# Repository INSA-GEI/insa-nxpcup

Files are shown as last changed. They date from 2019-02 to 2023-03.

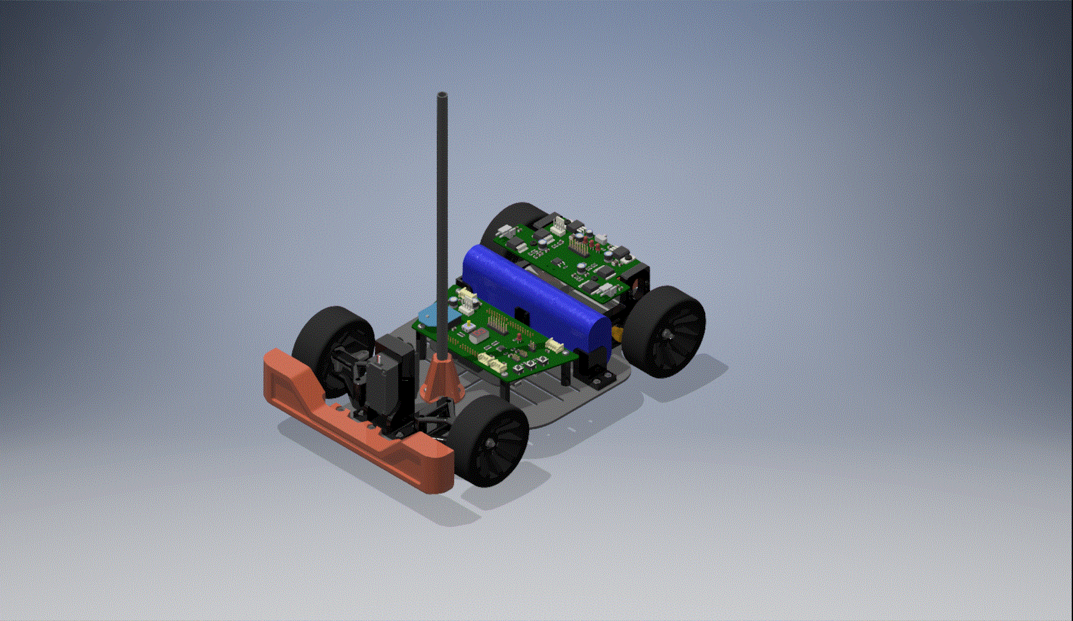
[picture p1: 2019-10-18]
meca/Inventor/Alamak.gif

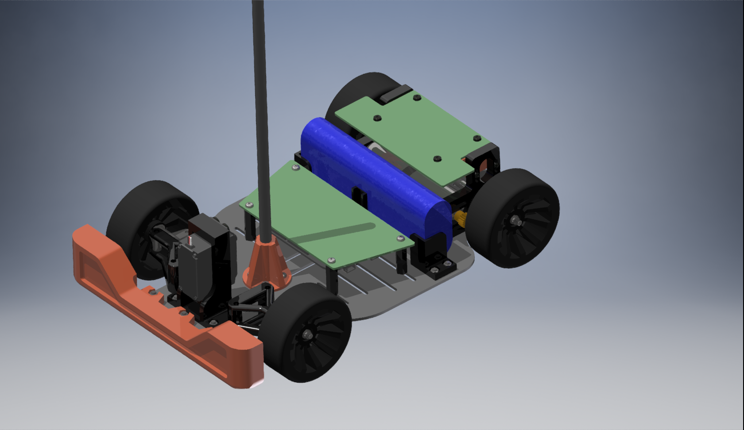
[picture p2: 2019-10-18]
meca/Inventor/Alamak.png

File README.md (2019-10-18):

# insa-nxpcup

Repository for INSA NXP cup 

# Where do I find/place the source code ?
Every folder titled `source_[...]` is a version of the code. One should only put the \*.c and the \*.h of the project, not the entire folder !

[...] Is a keyword or a_small_sentence describing this version in particular (e.g. "`source_dangerously_fast`" or "`source_safest`").

# Quick HowTo
Small survival kit for everyone : 
## Installing git (the clean way)
[Get here](https://git-scm.com/downloads) and follow the installer's instructions. One should avoid using github desktop client ;)

## Downloading the code
```bash
git clone https://github.com/INSA-GEI/insa-nxpcup-1.git
cd insa-nxpcup-1
```

## Update before you start working !
```bash
git pull 
```
If it doesn't work, save your changes elsewhere, and retry with
```bash
git stash	#Cancels all your changes in the repo
git pull	#Try pulling again
```

## Uploading your work
Upload as often as possible. Most errors here appear when working un un-updated code.
```bash
git commit -a #Prepare a commit with all updated files, ignoring new files.
git push #Sends the previous commit on this repo
```
**NB :** While commiting, use `Esc :wq Enter`. A good commit message is brief, and completes the following statement : *This commit will ...*.

# Branches management
**Do not use branches yet !**
Your are in branch master, nothing should be done here
Select a valid branch:

	git checkout int_team_1: Integration branch for team 1
	git checkout int_team_2: Integration branch for team 2

team work should use int_team_x branch as their main branch and integrate inside every stable work. Use development branch for your work in progress.

Old branchs:
	git checkout stable    : stable branch (Obsolete)
	git checkout dev       : work in progress (Obsolete)

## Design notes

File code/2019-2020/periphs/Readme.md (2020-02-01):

# Code de test des différents périphériques (low-level drivers) 
---
## test

Classe de debug ( UART OPENSDA, 7segment display, leds, rotary switch and pushbuttons).

Implémente un buffer circulaire et envoi par interruption.

##### TODO

* Solve issue with rotary switch missing counts -> check electrical continuity on pcb and correct port config
* Known issue with SW2 and BLUE_LED interferring : see pcb layout
* Extra : simplify usage of uart with a uart class in cpp

---
## Motor

Controle pwm des moteurs gauche et droit.

##### TODO

* Tabuler des vitesses en m/s pour diverses entrees en PWM (pour calibrer MOTOR_CAL_SPEED)

---
## Servo

Controle du servo avec limites d'angle.

##### TODO

* Check zero and max angle values

---

## encoder_v2

Retour de vitesse des roues

##### TODO

* Vérifier la bonne valeur de vitesse retournée par la classe pour une vitesse mesurée en réel

---

## Direction

Controlleur utilisant Motor, Servo, encoder_v2

##### TODO

* Calibrer coefficient entraxe
* calibrer correcteur KP
* vérifier la non saturation SPEED_LIMIT en fonctionnement normal

---
---

## Nom du dossier

Fonctions implementées

##### TODO

* Choses à faire
* ...

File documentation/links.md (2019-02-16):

# NXP community
* [git book nxp](https://nxp.gitbook.io/nxp-cup-hardware-reference-alamak/)
* [MCUXpresso example project with our board](https://github.com/ErichStyger/mcuoneclipse/tree/master/Examples/MCUXpresso/FRDM-KL25Z/MyMakeProject)
* [material ressources (sensors, motors, camera...)](https://community.nxp.com/docs/DOC-1284)
* [Landzo Alamak purchase website (for the fun)](https://www.aliexpress.com/store/product/Alamak-smart-car-competition-car-model-kit-CCD-camera-stand-base-Carbon-rod-bracket-8mm-base/428351_32817153828.html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)

# Misc.
* [ressources for robotics](https://github.com/Kiloreux/awesome-robotics#readme)

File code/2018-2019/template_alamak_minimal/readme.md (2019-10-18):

# Template alamak minimal 

Ce code est le template fournit par NXP permettant d'avoir une base en c pour tester la voiture

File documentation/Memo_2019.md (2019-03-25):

# Memo 2019
Voici nos notes à l'attention de l'équipe de l'INSA pour 2020. 

Il s'agit surtout d'une compilation de tous les problèmes que nous avons rencontré et qui auraient pu être évités.

## Problèmes de démarche et quoi faire

Pour avoir des informations concernant quoi faire, il ne faut absolument pas compter sur M.Tounsi. C’est mieux d’aller demander des infos à M.DiMercurio ou contacter kbkcao@etud.insa-toulouse.fr, saillan@etud.insa-toulouse.fr [ajoute des autres contacts]

Vous pouvez demander à M.Tounsi pour aller faire des tests de la voiture sur une piste à NXP de Toulouse. Normalement vous pouvez également emprunter les pistes et les ramener à l’INSA pour travailler avec. Nous avons travaillé en salle 113 puis salle 7.

## Problèmes de hardware

Les servos sur les voitures sont déjà remplacés par rapport à ce qui ont été utilisés en 2018. Les engrenages intérieurs des servos sont en métaux, plus costaud que ce que nous avions au début. Néanmoins, n’oublie pas de mettre des  pare-chocs en mousse devant les voitures quand vous travaillez à haute vitesse car une collision violente quand les voitures rament contre les murs, meubles, etc.... peut casser les engrenages intérieurs du servo.

Les cartes et les caméras sont assez fragiles et peuvent être facilement cramés donc il faut faire attention. Normalement M.DiMercurio peuvent refaire des PCB pour remplacer avec les schémas si ca n’est pas fait.

Il faut vérifier la transmission entre les moteurs et les roues derrières (pas trop serré car les moteurs pourront pas démarrer, mais si c’est pas assez proche il y aura pas de transmission).

L’idéal sera de changer les engrenages entre roues/moteurs. Pour l’instant il y a des engrenages plastiques contre d’autres en métaux. Il faudrait que tous soient au final en métal.

Il faut faire attention aux mâts de caméras, il faut vraiment fixer les caméras avant des faire les tests afin qu’elle ne tremble pas (sinon vous allez perdre de temps sur des trucs qui marchent par hasard). Il faut vraiment demander à M.Tounsi et M.DiMercurio pour faire en sorte que vous avez assez de voitures pour tester. Supposant que vous êtes aussi 3 équipes, il vous faut 3 voitures, et nous espérons de les voitures de notre année soient bien préservés pour que vous puissiez les ré-utiliser.

L’idéal est de vérifier le fonctionnement de la caméra avec un script simple sur matlab, il est également conseillé de bien faire la mise au point. Il est aussi possible de regarder les données renvoyées par la caméra en oscilloscope mais ca va être très difficile et ca marche pas tout le temps, donc c’est la dernière option. 

## Problèmes de software

Le caméra renvoie un array de 128 int de donnés. Pour visualiser “en live” le caméra il faut avoir une version Matlab craqué (version Matlab acheté il faut acheter le add-on Simulink Coder qui va couter 20e en plus, et on n’est pas trop sur quel autre add-on sera nécessaire) avec Simulink coder et les support packages faits pour le NXP cup. Concrètement les 3 add-ons: 

- NXP Cup Companion
- Simulink Coder Support Package for NXP FRDM-KL25Z Board
- NXP FRDM-KL25Z Support Package Update

Pour télécharger les packages il vous faut un compte Matlab. Ca marche même si vous avez un Matlab craqué. 
Par contre ca sera très difficile de faire marcher de manière optimale la voiture avec un program Matlab/Simulink, pour ca il faut vraiment hard-code un programme en C. Normalement les codes sont disponibles sur la page github de GEI.

Dernier point concernant l’histoire Matlab, il va vous sembler inutile de passer tous ces étapes juste pour visualiser les données du caméra, mais c’est très pratique: si qqch ne fonctionne pas, vous pouvez toujours voir ce que renvoie le caméra et fait un diagnostique en moins de 5 mins et vous serez pas bloqué des jours sur un caméra qui fonctionne pas.

Si vous travaillez sur une machine virtuelle Windows, les données observés avec le caméra sera pas très fiables. Il y a des guides et un fichier pré-fait pour observer les données du caméra dans les fichiers des add-ons. 

Pour programmer en C, il faut CodeWarrior. Vous pouvez trouver la version nécessaire ici: https://www.nxp.com/support/developer-resources/software-development-tools/codewarrior-development-tools/downloads:CW_DOWNLOADS 
Choisir la version: CodeWarrior® for MCUs (Eclipse IDE), version 11.1, Special Edition. Ce n’est pas payant et il faut juste faire un compte NXP. 

Les programmes qui fonctionnent sont normalement sur Github de GEI, NXP Cup et vous pouvez demander à M.DiMercurio de vous ajouter pour avoir accès à ces fichiers. Il est fortement conseillé de savoir utiliser le github car nous ne l'avons pas assez utilisé et c’est un peu un bordel le projet. Gros avantage de Github: dès que vous avez un truc qui fonctionne bien et vous êtes satisfait, faites un push avant de continuer car **LE MÊME CODE VA PAS FONCTIONNER PAREIL APRÈS 30 MINS ET QUELQUES CHANGEMENTS DE VARIABLES.** N'hésitez pas à rajouter 'STABLE' dans votre message de commit quand le code marche.

## Problèmes liés aux tests

Il faut nettoyer les roues de la voitures et les pistes/ la salle car le frottement va beaucoup changer le comportement de la voiture. Si vous travaillez en salle 7 (qui est très salle et a beaucoup de poussière), il faut passer aspirateur ou passer un coup de balaie, ensuite nettoyer la salle avec une serpière pour réduire au minimum la poussière). Comme ca on peut être sur que les roues va adhérer à la piste. Il faut faire le nettoyage régulièrement!! (au début de votre séance de test). Niveau de propreté recommandé: vous pouvez marcher à pieds nus confortablement dans la salle. 

Comme mentionné avant, il faut faire attention quand on fait des testes à haute vitesse car ca peut endommager des servos quand les voitures rament contre les meubles, la voiture peut passer en dessous les meubles et il y a des barres qui va casser les mâts de caméras. Les mâts peuvent être refaits mais les caméras sont un peu cher et difficile de retrouver (nous avons du aller sur eBay pour trouver un remplacement) et donc il faut faire attention. 

Il y a beaucoup de paramètres qui influencent le comportement de la voiture (les seuils pour détection des gradients de luminosité, les valeurs de correcteurs, combien de correcteurs, frottement, etc...) Change un seul truc à la fois et voit comment comporte la voiture. Avoir aussi des priorités, par exemple: si vous êtes pas surs que vos caméras fonctionnent correctement et plus ou moins résilients contre les variations de luminosité, si votre servo n’est pas bien polarisé, etc... ca vaut pas la peine d’aller chercher les paramètres de correcteurs car ca va pas remarcher. 

C’est normal qu’un truc qui fonctionne aujourd’hui ne fonctionne plus le lendemain (même au bout d’une heure). Il faut vraiment aller chercher pourquoi et régler le problème pour vraiment bien avancer.

## Recommandations

Ajouter un panneau de LEDs pour éclairage, ca va aider à régler le problème de seuil de caméra. L’idéal est d’avoir une forte lumière rouge pile à l’endroit qu’observe la caméra. Cela vous permettra d’avoir un programme robuste qui fonctionnera peut importe l’éclairage ambiant. (nous sommes partis du principe que l’éclairage lors de la compétition serait optimal et cela a été une grosse erreur).

On a des encodeurs pour avoir une régulation de vitesse. Ca peut beaucoup améliorer votre commande de vitesse mais ne perdez pas trop de temps là-dessus si vous arrivez pas.
Il peut être très pertinent d’utiliser 2 caméras (une qui regarde loin et une qui regarde proche). Cela permettra d’aller encore plus vite en ligne droite tout en anticipant les prochains virages.

Si vous avez du temps, vous pourrez peut être étudier comment utiliser une caméra 2D. Un exemple c’est le ligne d’arrivé qui peut être très difficile à détecter avec une seule caméra ligne. 

Vous pouvez ajouter des autres capteurs pour finir des challenges (si il y a encore des challenges pour NXP Cup 2020). Ex : capteur de distance

Il peut être intéressant d’utiliser les accéléromètres présents sur le microcontrôleurs. Cela permettra de détecter le passage d’un “bump” et d’ignorer les données inexploitables renvoyées par la caméra à ce moment là

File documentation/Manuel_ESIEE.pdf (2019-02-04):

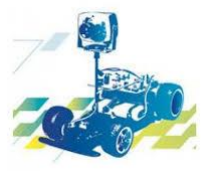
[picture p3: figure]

# Guide de de marrage et de de veloppement pour la NxP Cup

Pour châssis Model-C et carte microcontrôleur FRDM KL25Z

T. Grandpierre (t.grandpierre@esiee.fr)

T. Grandpierre © / ESIEE | 2

T. Grandpierre © / ESIEE | 3

## Remerciements

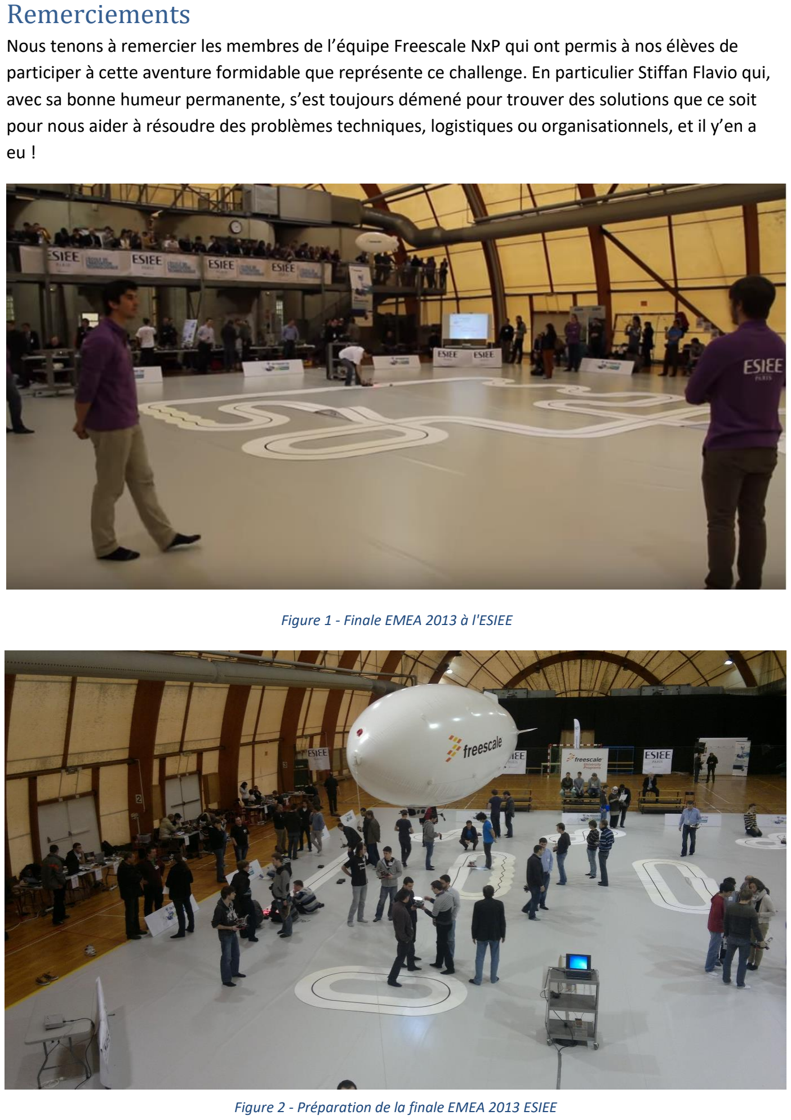
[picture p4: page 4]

Nous tenons à remercier les membres de l’équipe Freescale NxP qui ont permis à nos élèves de participer à cette aventure formidable que représente ce challenge. En particulier Stiffan Flavio qui, avec sa bonne humeur permanente, s’est toujours démené pour trouver des solutions que ce soit pour nous aider à résoudre des problèmes techniques, logistiques ou organisationnels, et il y’en a eu !

Figure 1 - Finale EMEA 2013 à l'ESIEE

Figure 2 - Préparation de la finale EMEA 2013 ESIEE

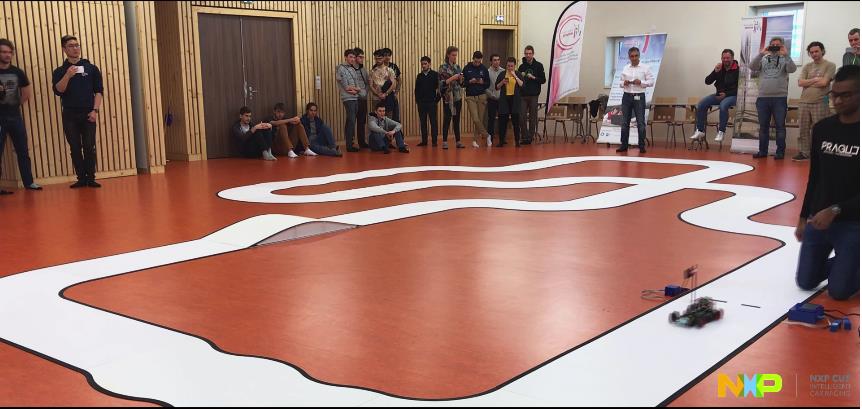
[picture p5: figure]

T. Grandpierre © / ESIEE | 5

## Introduction

### Présentation

La NxP Cup est une compétition mondiale qui commence par des sélections dans chaque continent. C’est une course de voiture miniatures autonomes sur un circuit qui n’est pas connu à l’avance. Le circuit est matérialisé par deux lignes noires tracées sur une bande blanche. Il peut y avoir des croisements, des ponts, des ralentisseurs, des tunnels.

Le châssis (groupe de propulsion et direction) est imposé, mais le choix de la carte de contrôle (microcontrôleur NxP) et des capteurs est libre. L’objectif est donc de construire une voiture qui soit autonome et roule le plus vite possible en détectant la piste.

Figure 2 - Vidéo complète : https://perso.esiee.fr/~antonraj/mes_projets/Nxp_cup/wp-content/video/nxp_cup_2018_esiee.mp4

La page principale de présentation de la NxP Cup où toutes les infos sont données : https://community.nxp.com/groups/tfc-emea

EMEA : region Europe, Middle-East (Moyen-Orient), Africa.

### Intéret pédagogique

- Travailler en équipe
- Réalisation complète

T. Grandpierre © / ESIEE | 6
- Prog. des microcontrôleurs (langage C) + programmation PC
- Electronique (contrôle moteur, caméra, radio...)
- Apprendre à résoudre des problèmes concrets
- Sujet transversal, robotique
- Autonomie
- Découverte, contacts avec le monde industriel, les contraintes, les délais

### Principe

Il faut identifier en temps réel les bords de la piste qui sont tracés en noir sur fond blanc. Il existe plusieurs solutions pour cela : utilisation de caméras noir et blanc ou couleur, utilisation de caméras linéaires, utilisation d’une barre de capteur infra-rouge…

L’utilisation d’une barre est peu appropriée car encombrante. En effet elle doit être disposée juste au-dessus de la bande noire, de plus la sensibilité et la précision seront assez faible.

L’utilisation d’une caméra 2D standard noir et blanc ou couleur est idéale mais demande une relativement forte puissance de calcul embarquée ainsi que de la mémoire RAM pour stocker la ou les images : jusqu’en en 2017 seul certain microcontrôleurs étaient autorisés ce qui limitait cette possibilité relativement complexe.

L’utilisation d’une caméra linéaire est très adaptée, elle est fournie dans le kit de démarrage NxP.

### Kit de démarrage NxP

Jusqu’en 2017, le seul châssis autorisé était le « modèle-C », celui dont on dispose à l’ESIEE :

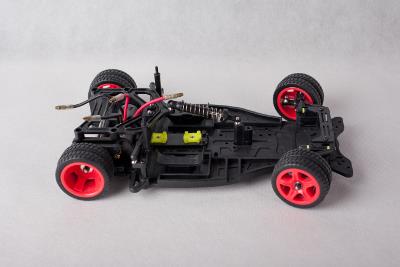
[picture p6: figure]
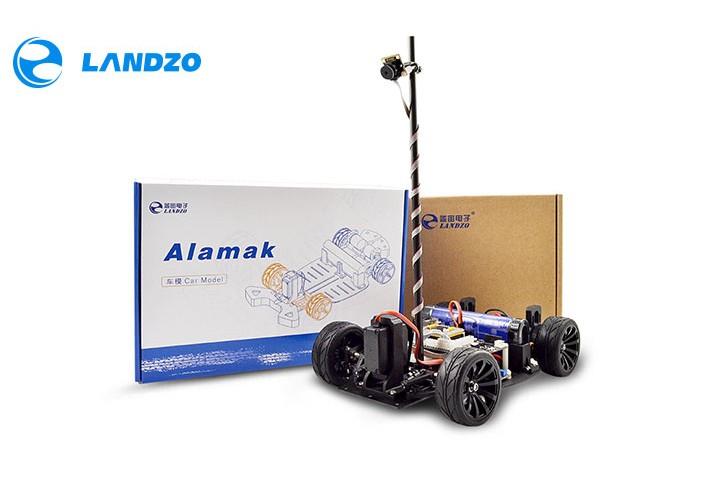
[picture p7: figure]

T. Grandpierre © / ESIEE | 7

Figure 3- Châssis "Model C"

Depuis 2017 un nouveau châssis a vu le jour et fait l’objet d’une course spécifique, le modèle « Alamak » :

Figure 4- Châssis « Alamak »

Ces châssis comportent 2 moteurs à balais 7.2v maximum pour la propulsion et un servomoteur standard de modélisme pour la direction.

Pour piloter le servo et les moteurs, NxP a développé des cartes d’interface de puissance (2 versions successives pour le modèle C et une nouvelle version pour le modèle Alamak). Ces cartes offrent les mêmes fonctionnalités : elles comportent des ponts en H pour la commande des moteurs de propulsion et la connectique pour une ou deux caméras linéaires et pour un ou deux servo de direction.

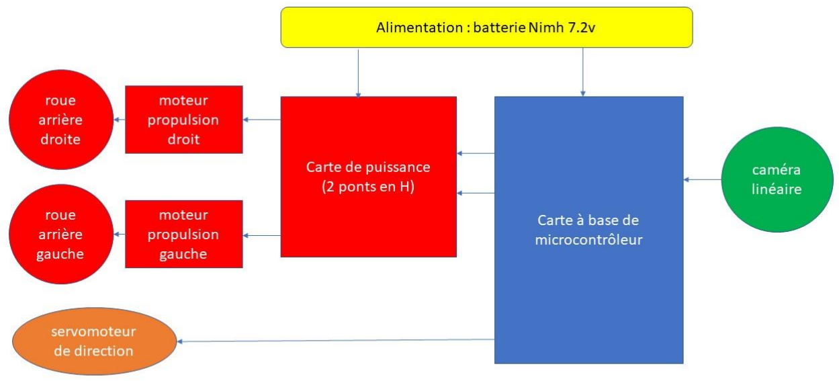
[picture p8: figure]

T. Grandpierre © / ESIEE | 8

Enfin, pour « l’intelligence » de la voiture, NxP propose plusieurs kits de développement à base de leurs microcontrôleurs : Kinetis FRDM-KL 25Z, TWR-K40X256, Qoriva MPC-5604B, K40 KwikStik…

La page suivante regroupe des liens vers les différentes options possibles pour le matériel : https://community.nxp.com/docs/DOC-1284

### Architecture d’une voiture

Un véhicule est donc composé au minimum des éléments suivants :

- Un châssis « Alamak » ou « model C »
- 2 moteurs de propulsion
- 1 servo de direction
- Une carte de puissance pour les moteurs de propulsion
- Une caméra linéaire
- Une carte microcontrôleur
- Une batterie Nimh 7.2v 2500mAh max (imposé)

Figure 5 -Architecture fonctionnelle de la voiture

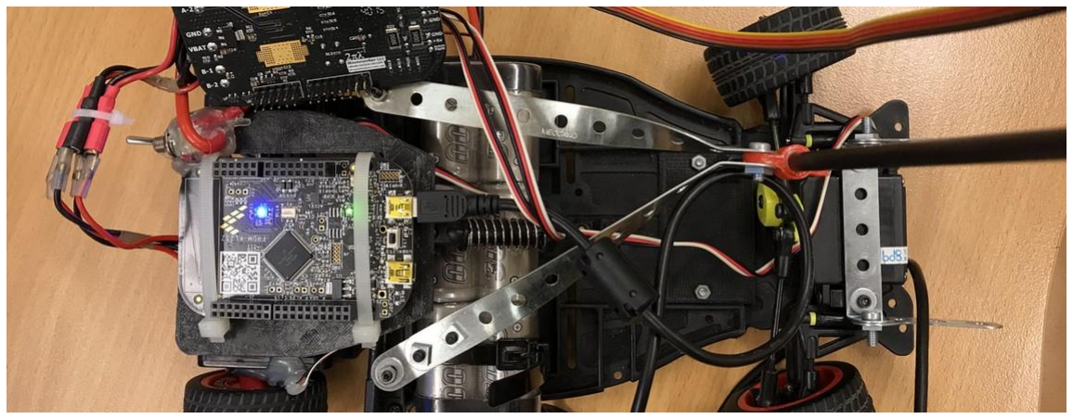
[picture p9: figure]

T. Grandpierre © / ESIEE | 9

Choix du matériel ESIEE :

- Châssis « modèle C »,
- Cartes microcontrôleurs FRDM-KL25Z (et KL46Z plus puissantes dont les connecteurs sont compatibles),
- Cartes filles de puissance compatible FRDM-KL25Z (rev. 1 : https://community.nxp.com/docs/DOC-1059 )
- Caméra linéaire « TAOS 1401 » ( https://community.nxp.com/docs/DOC-1030 )

Figure 6 - Carte KL25Z sur châssis « modèle C »

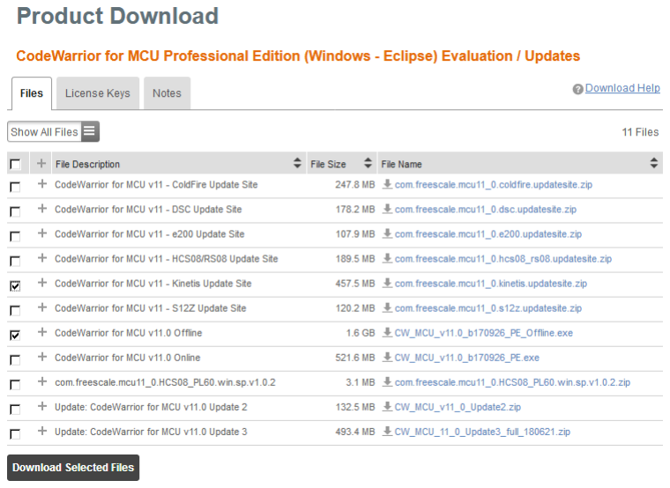
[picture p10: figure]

T. Grandpierre © / ESIEE | 10

## Prise en main Kinetis KL25Z

Avant de pouvoir utiliser la carte de développement FRDM-KL25Z, nous commençons par présenter l’installation de l’environnement, puis nous présentons la carte, comment la configurer avant de terminer par la présentation d’un exemple complet qui fait clignoter ses leds.

### Environnement de développement logiciel

Sous windows : 3 grandes possibilités Code Warrior (l’IDE Freescale), Kinetis Studio, ou Keil-MDK µVision. Ils permettent tous de saisir du code C/asm, de le compiler, de le télécharger sur le micro, de faire du débug pas à pas.

1. Code Warrior 10.6, 10.7 ou 11 (« CW ») : c’est l’outil de dev. Freescale/NxP , l’avantage quand on l’installe c’est que l’on va disposer des exemples freescale pour chacune des cartes. Les versions 10.6 et 10.7 sont les anciennes versions de CW (voir 2.) utilisées pour créer les exemples pour la voiture. La version 11 semble aussi le permettre, à vérifier.
a. « CodeWarrior 11 » est téléchargeable en version d’évaluation ici : https://nxp.flexnetoperations.com/control/frse/download?element=9346447
Il faut sélectionner l’extension pour Kinetis :
b. « CodeWarrior MCU v10.6 Evaluation Edition » la version complète limitée à 1 mois qui devient limitée en taille de binaire généré quand le mois est écoulé.
c. « CodeWarrior MCU v10.6 Special Edition » la version illimitée en durée mais limitée en taille. Je vous conseille d’utiliser celle-ci, puis plus tard si vous êtes limité par les 128Ko ( !!), d’installer la version Evaluation Edition.
Remarque importante : les versions CW 10.6 et 10.7 ont été conçues avant Win7, le répertoire d’installation des programmes s’appelait alors « c:\Program Files », il n’y

T. Grandpierre © / ESIEE | 11

avait pas de répertoire « c:\programme file x86 » dans lequel s’installent par défaut tous les softs 32bits => ATTENTION si possible installer CW dans c:\Program Files car si il est installé ailleurs des exemples risquent de ne pas fonctionner car les includes sont parfois codés en dur. Cependant pour mes tests tout s'est bien passé en l'installant dans c:/freescale/CW etc.

2. Kinetis Studio : il a été un temps le successeur de CodeWarrior pour la gamme des microcontrôleurs Kinetis, mais je pense finalement en voie d’abandon pour revenir à CodeWarrior 11.0 for MCU
3. Keil MDK µVision est l’outil supporté par ARM pour tous les micros de la famille des cortex M : Freescale (Kinetis), NXP (LPC), STM (32F 32L), Texas Instrument (Stelaris, Tiva) etc.). Son IDE est très simple et très rapide à prendre en main (c’est celui que nous utilisons pour nos TPs d’introduction aux Cortex M à l’ESIEE en première année). Comme CW, il existe en version limitée (MDK-Lite) en taille de code généré mais seulement 32Ko (ce qui est quand même largement suffisant pour les premiers projets). Il est téléchargeable depuis cette page, il faudra remplir un formulaire : http://www.keil.com/arm/mdk.asp Il est intéressant de le connaitre pour passer d’un constructeur à l’autre. De plus, il est fourni avec au moins un exemple (clignotement d’une led) pour quasiment toutes les cartes de dev. de tous les constructeurs. Il est aussi très intéressant en pédagogie car il contient aussi un simulateur assez complet permettant entre autre de voir les GPIO et autres périphériques (attention cependant, ce simulateur n’existe pas pour toutes les variantes de micro/constructeur, pour un constructeur donné il faut chercher la référence de la variante pour laquelle il existe un simulateur).

Le projet de démonstration fournit par NxP pour tester la voiture étant sous Code Warrior, nous choisissons donc

### Présentation de la carte de développement « Freedom » FRDM-KL25Z

Le microcontrôleur à programmer est au centre « KL25Z ». « 80 LQFP » correspond au type du boitier (LGFP) et au nombre de broches (80). Il est en effet plusieurs variantes de ce processeurs avec plus ou moins de broche et donc des types de boitiers plus ou moins gros.

Pour mieux comprendre cette carte il faut analyser son manuel utilisateur et ses schémas disponibles dans l’archive suivante (chercher « frdm kl25z sur le site NxP), puis cliquez sur « User Guide »:

https://www.nxp.com/support/developer-resources/evaluation-and-development-boards/freedom-development-boards/mcu-boards/freedom-development-platform-for-kinetis-kl14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 (https://www.nxp.com/support/developer-resources/evaluation-and-development-boards/freedom-development-boards/mcu-boards/freedom-development-platform-for-kinet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)

T. Grandpierre © / ESIEE | 12

Figure 7- Carte FRDM-KL25Z -Vu côté composants

On constate que la carte comporte :

- une led RGB (constituée de trois leds dans un même boitier),
- un capteur inertiel MMA8451Q (accéléromètre)
- un « slider » tactile capacitif (en haut)
- 2 connecteurs USB,
- 4 connecteurs d’entrées-sortie de chaque côté (J1, J2, J9 et j10).

Le rôle de ces connecteurs est récapitulé dans la figure page 14 :

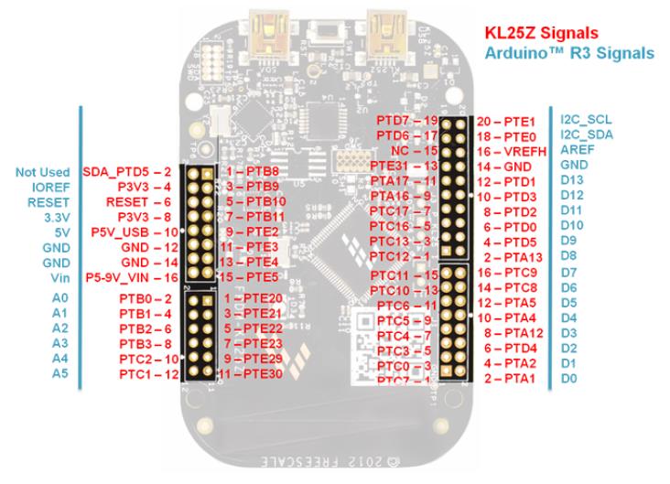
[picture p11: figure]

T. Grandpierre © / ESIEE | 13

On constate ainsi que la disposition des broches est faites pour être compatible (en bleu) au maximum avec le brochage des cartes filles (« shield ») Arduino.

Le « block diagram » (figure suivante extraite de la page 4 du « user manual ») nous apprend que le KL25Z est un KL25Z128VLK4 80 LQFP », et qu’il est alimenté par les deux connecteurs USB par le biais d’un convertisseur 3,3v à faible perte (en rouge) mais alimentable aussi par l’un des connecteurs (vin).

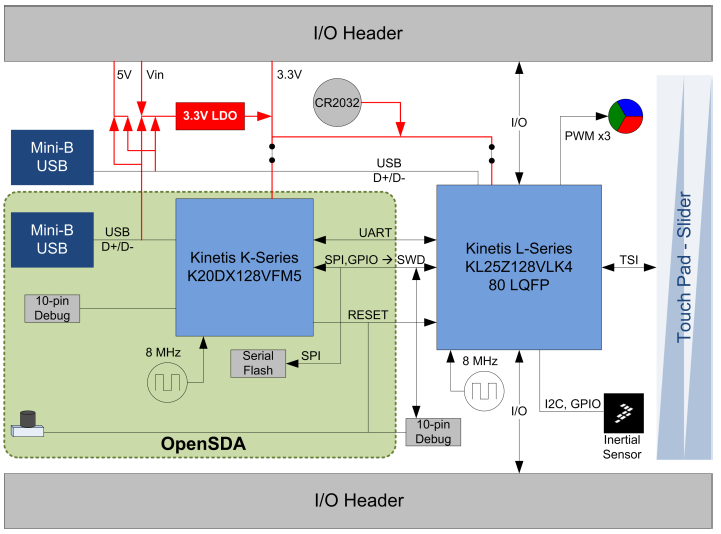
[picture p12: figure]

T. Grandpierre © / ESIEE | 14

Figure 8 - Architecture de la carte FRDM-KL25Z

On y découvre aussi que les cartes Kinetis possèdent une interface de débogage incorporée : via une connexion USB entre le PC (qui exécute Code Warrior) et la carte il est possible de télécharger du code dans la RAM ou la FLASH du microcontrôleur KL25Z et ce sans matériel supplémentaire. C’est la partie sur fond vert de la figure ci-dessus suivante.

Cette interface de programmation fonctionne selon un protocole série appelée « OpenSDA ». Il utilise un autre microcontrôleur (K20DX128VFM5) dédié à cet usage uniquement. Pour travailler sur cette carte depuis le PC il faut donc connecter un câble USB entre le PC et le connecteur USB mini marqué « OpenSDA » (c’est-à-dire celui de droite sur la photo page précédente).

### Configuration de la carte pour mode debug

Par défaut, quand la carte est neuve la carte elle est préprogrammée avec une démo qui fait varier les couleurs des leds en fonction de la position spatiale de la carte, mesurée à l’aide du capteur inertiel.

De plus, en connectant cette carte au PC (après avoir éventuellement installé les drivers) on constate que le microcontrôleur secondaire (K20DX128) n’est pas en mode OpenSDA mais émule une carte mémoire ( firmware « mass storage ») : la carte est alors vue par le PC comme une clef USB. C’est très intéressant car pour placer une application dans la carte depuis windows il suffit de copier/coller le binaire de cette application (fichier d’extension .sc) dans cette « clef usb ». C’est donc très simple, NxP fournit ainsi plusieurs programme compilé dans le sous-répertoire « Precompiled Examples » de

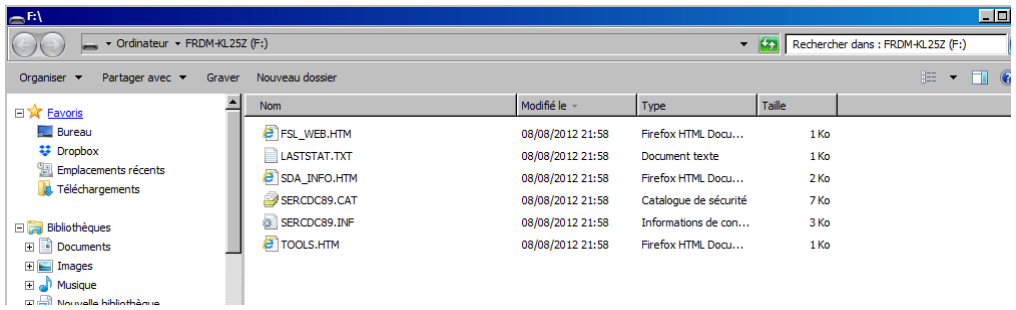
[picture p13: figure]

T. Grandpierre © / ESIEE | 15

l’archive « FRDM-KL25Z Quick Start Package » téléchargeable sur la page NxP dédié à cette carte. Remarque : ne pas copier directement les fichiers entre l’application d’archivage et la clef, il est préférable de d’extraire les fichiers avant de la placer sur la carte.

Figure 9 - FRDM-KL25Z vue par le PC comme une clef USB de même nom

En revanche dans ce mode, il n’est pas possible de faire du débogage. Pour la passer en mode débogage « OpenSDA » il faut reflasher le firmware du microcontrôleur K20 (pas le KL25Z) de la carte, ceci compte plusieurs étapes :

1. Tout d’abord il faut récupérer le firmware qui est développé par PEMICRO (partenaire de NxP). Le lien peut être obtenu en cliquant directement sur le fichier « SDA_INFO.HTM » présent sur la carte (voir figure précédente) , ou bien en allant sur leur site : http://www.pemicro.com/opensda/index.cfm Il faut alors télécharger le fichier archive de la section « OpenSDA Firmaware » (« Firmware Apps ») : Pemicro_OpenSDA_Debug_MSD_Update_Apps..date...zip. Cette archive contient les firmwares pour plusieurs cartes de développement, il faut extraire les 2 fichiers qui correspondent à notre FRDM-KL25Z, c’est-à-dire : DEBUG-APP_Pemicro_v108.SDA et si besoin MSD-DEBUG-FRDM-KL25Z_Pemicro_v118.SDA qui est le firmware d’origine si l’on voulait remettre la carte dans le mode « Mass Storage ».
2. Ensuite il faut placer la carte en mode « Firmware update », pour cela :
a. Débrancher le câble USB de la carte
b. Appuyer sur le bouton poussoir de la carte
c. Reconnecter le câble USB sur le même port USB (OpenSDA) en maintenant toujours le bouton poussoir appuyé
d. Relâcher le bouton poussoir après quelques secondes
3. La carte devrait être vu maintenant comme une clef USB dont le nom n’est plus KL25Z comme précédemment, mais « BOOTLOADER »

T. Grandpierre © / ESIEE | 16

Figure 10- La FRDM-KL25Z apparait comme une clef USB « BOOTLOADER »

4. Il suffit de placer le fichier de firmware (DEBUG-APP_Pemicro_v108.SDA) sur ce nouveau lecteur, attendre 1 minute pour être certain que la mise à jour s’effectue,
5. puis brancher/rebrancher l’USB (sans appuyer sur le poussoir puisque le firmware est maintenant à jour).
6. Cette fois, plus aucune fenêtre ne doit s’ouvrir, la carte n’est plus vue comme une clef USB mais comme une interface de programmation OpenSDA (voir ci-dessous), mais pour cela il peut être nécessaire d’installer le driver windows de cette interface de programmation OpenSDA : sur la même page PEMICRO où les drivers ont été trouvés, il y a une rubrique
« Windows USB Drivers » avec un exécutable (.exe) qu’il faut exécuter. Débrancher la carte avant de l’exécuter.
7. Il est toujours préférable de s’assurer que la carte est bien configurée en mode OpenSDA et que le driver est bien installé. Pour cela il faut ouvrir le « gestionnaire de périphériques » (taper son nom dans la barre de recherche windows), et dans la rubrique « Ports (COM et LPT) » vous devez voir apparaitre « OpenSDA » ainsi que le numéro de port série associé (COM35 dans la capture ci-dessous) :

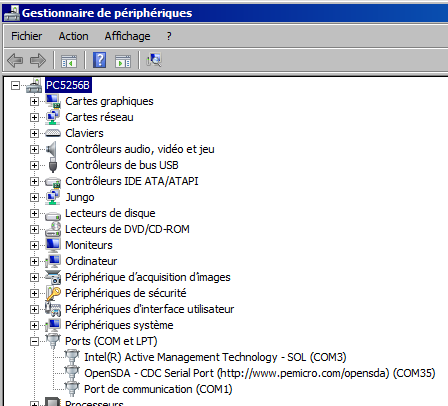
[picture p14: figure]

T. Grandpierre © / ESIEE | 17

Figure 11- Gestionnaire de périphériques

REMARQUE WINDOWS 10 : sous windows 10, en fonction des versions, il se peut que les transferts vers la carte ne fonctionne pas, que ce soit en mode « Mass Storage » ou en mode de mise à jour du bootloader. Cela est dû au fait que windows 10 créé des fichiers cachés d’indéxation et qu’ils sont aussi copiés sur la carte. Pour que cela fonctionne sous windows 10, il faut utiliser une des trois solutions suivantes après avoir lancé le gestionnaire de services (« services.msc »), puis désactivé le service de stockage et windows search :

- 1

ère possibilité : éditeur de statégie

Lancer l’éditeur de stratégie (« gpedit.msc »), puis aller dans « Config. De l’ordinateur »➔ « modèle d’administration »➔composants windows ➔ Rechercher et cliquer sur la politique « Ne pas autoriser d’emplacement sur les disques amovibles aux bibliothèques », activer cette politique et OK. Redémarrer le PC.

- 2

ème possibilité : éditeur de registre

Lancer l’éditeur de registre (« regedit »), puis chercher l’une clefs « search » ou « windows search » qui contient la propriété « DisableRemovableDriveIndexing » qu’il faut passer à 1.

T. Grandpierre © / ESIEE | 18

Si elle n’existe pas vous pouvez la créer dans "HKEY_LOCAL_MACHINE\SOFTWARE\Policies\Microsoft\Windows Search". Puis ajouter une clef nommée "DisableRemovableDriveIndexing" avec le type "REG_DWORD" et la placer à
1. Redémarrer le PC.
- 3

ème possibilité : trouver une machine windows 7 pour changer le firmware en OpenSDA. Une fois le changement effectué, il n’y a plus de problème liés à windows 10.

(voir https://os.mbed.com/users/maripogoda/notebook/update-frdm-kl25z-bl-with-win8/ pour des informations complémentaires).

### Premier programme « From Scratch » avec Code Warrior

Lancer Code Warrior. Comme tous les outils basés sur l’environnement Eclipse il vous demande de choisir l’emplacement d’un espace de travail « worspace », vous pouvez laisser celui par défaut ou le renommer par exemple « KL25Workspace ». Ainsi vous pourrez switcher d’une espace à un autre facilement si vous avez plusieurs projets.

Ensuite il suffit de créer un nouveau projet : menu new→BareBoard Project et choisir le processeur qui correspond à la carte cible en regardant sa référence, tout simplement :

Figure 12- Reference du processeur KL25Z128

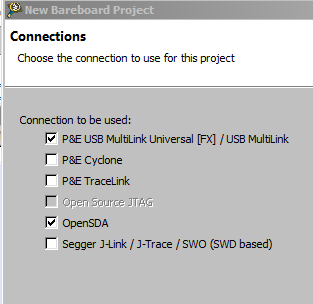
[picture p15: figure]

T. Grandpierre © / ESIEE | 19

Choisir ensuite la connexion OpenSDA

Puis laisser les configurations proposées par défaut sur les onlgets qui suivent jusqu’à cliquer sur « Finish ».

Code Warrior génère alors un projet de base avec un fichier main.c contenant une boucle infinie :

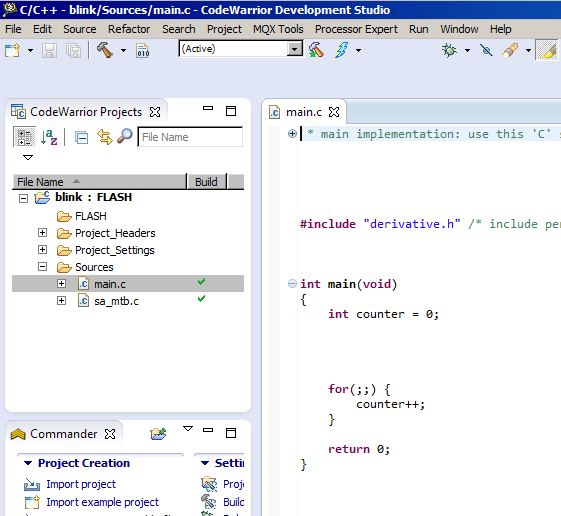
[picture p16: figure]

T. Grandpierre © / ESIEE | 20

Vous devez pouvoir le compiler sans erreur en cliquant sur le marteau de la barre de menu. Il faut ensuite le transférer dans la mémoire de votre carte en cliquant sur le petit insecte vert. CW communique alors avec votre carte (qui doit être connectée par USB !), prend le contrôle du processeur et y télécharge votre programme dans sa mémoire RAM. Cliquer enfin sur le rectangle vert pour lancer l’exécution. Bravo, le programme tourne….mais comment le savoir ? Faites pause (bouton à gauche du rectangle rouge) . Ceci stoppe le processeur et lit la valeur des variables de votre programme (la valeur de counter s’affiche en haut à droite) :

et une flèche vous indique là où s’est arrêté le processeur :

T. Grandpierre © / ESIEE | 21

Vous pouvez relancer/arrêter à nouveau pour vérifier les incréments du compteur :

Figure 13- nouvelle valeur du compteur

Oui, il compte très vite : à 48 MHZ !

Vous pouvez mettre fin à la session de debbug en cliquant sur le rectangle rouge, puis revenir dans le projet en cliquant sur « C/C++ » dans la barre du haut à droite.

Notez que ce programme inclut un fichier « derivative.h » qui lui-même inclut un fichier
<MKL25Z4.h> (faites simplement un clic droit sur le nom pour ouvrir le fichier). Parcourez ce dernier pour découvrit qu’il contient les définitions des adresses de tous les registres internes du processeur, cela va s’avérer très pratique pour la section suivante !

### Faire clignoter une led

C’est le « hello world » de l’embarqué, on commence souvent par allumer une led pour tester la chaîne de développement. Sur cette carte il y a 3 leds dans un même boitier, choisissons de faire clignoter la rouge (vous pourrez changer facilement !).

Pour l’allumer, il faut l’identifier sur le schéma du « User manual » de cette carte ( p.13) ou directement dans le pdf contenant ces schémas : FRDM-KL25Z_SCH_REV_E.pdf page 3 en bas à gauche :

T. Grandpierre © / ESIEE | 22

Les leds rouge, verte et bleu sont respectivement connectées sur le bit 18 du port B, le bit 19 du port B et le bit1 du port D.

En suivant le nom du fil on trouve même le numéro des broches du KL25Z : 53 pour PTB18 et 54 pour PTB19.

En cherchant cette broche sur la data sheet page du processeur (KL25P80M48SF0.pdf), on découvre (p48 de KL25P80M48SF0.pdf et dans la colonne « 80 LQFP » puisque c’est le suffixe de la référence de notre processeur soudé sur cette carte, cela correspond au nombre de broches) que cette broche peut être configurée pour l’une des deux fonctions : PTB18 (colonne ALT1) ou TMP2_CH0 (colonne ALT 3).

En effet, en lisant le référence manuel (KL25P80M48SF0RM.pdf ) et en particulier le chapitre 11 « Port control and interrupts) , on découvre qu’il est possible de choisir le périphérique auquel on veut connecter la broche en fonction de la valeur « ALT » qu’il faut placer dans les bits 10 à 8 du registre « Pin Control Register n », communément appelé « PORTx_PCRn » (p184).

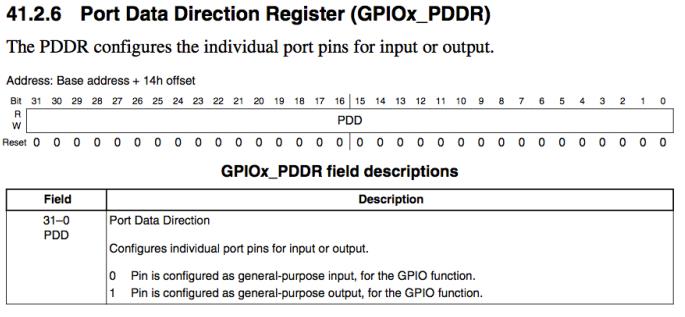
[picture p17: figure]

T. Grandpierre © / ESIEE | 23

On découvre que PTC13 correspond au rôle de broche d’entrée-sortie à usage générale : GPIO. Le chapitre 41 du reference manual est dédié aux entrées-sorties. On y découvre que les broches sont regroupées par paquets de 32, pour former des ports : port A, port B, port C etc. (le nombre de port dépend du microcontrôleur, de son boitier etc.). La broche 53 nommé PTB18 fait donc partie du port GPIO B, bit 18.

Il nous faut ensuite indiquer dans le registre GPIOx_PDDR si cette broche est une entrée ou une sortie. Les informations ci-dessous, toujours tirées du reference manual nous indique que par défaut toutes les broches sont configurées en entrées (0 au reset). Il nous faut donc placer le bit 18 à 1 (en sortie).

Figure 14- Direction p.778

Grâce aux macros qui existent dans le fichier d’include du projet crée on peut directement écrire :

GPIOB_PDDR = (1<<18) ;

Ensuite pour allumer la led rouge il suffira d’activer (mettre à 1) le bit correspondant grâce au registre GPIOx_PDOR

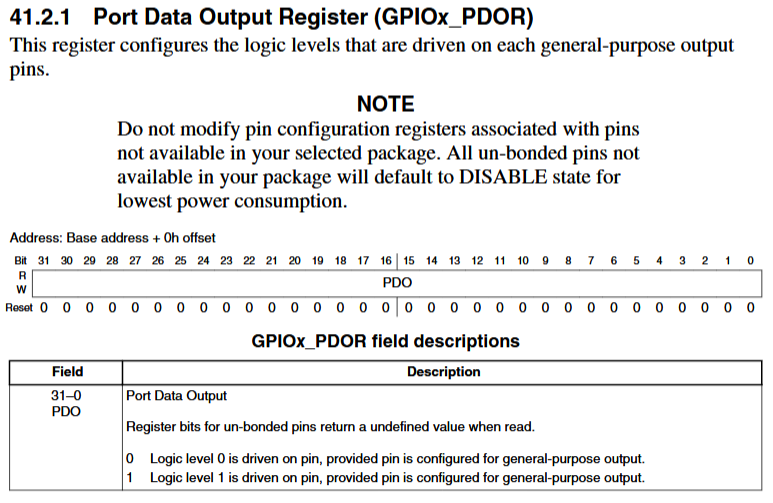
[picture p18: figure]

T. Grandpierre © / ESIEE | 24

Figure 15- Output p775

Mais il y a encore mieux : il est possible de faire un « toggle » (une inversion) de l’état d’une broche en utilisant le registre GPIx_PTOR : (ce type de registre n’existe pas sur tous les microcontrôleurs !)

Figure 16- Toggle, p777

Nous avons presque tous les élément necessaire pour faire clignoter une led, mais une chose importante reste à faire pour pouvoir utiliser le port B : l’activer !

En effet, par défaut au demarrage du processeur, la plupart de ses périphériques sont désactivés pour minimiser sa consommation électrique. La page 206 du reference manual nous explique que pour activer les périphériques il suffit d’activer un bit dans le registre SIM_SCG5. Ceci a pour effet de piloter un multiplexeur qui fait arriver l’horloge sur le périphérique voulu :

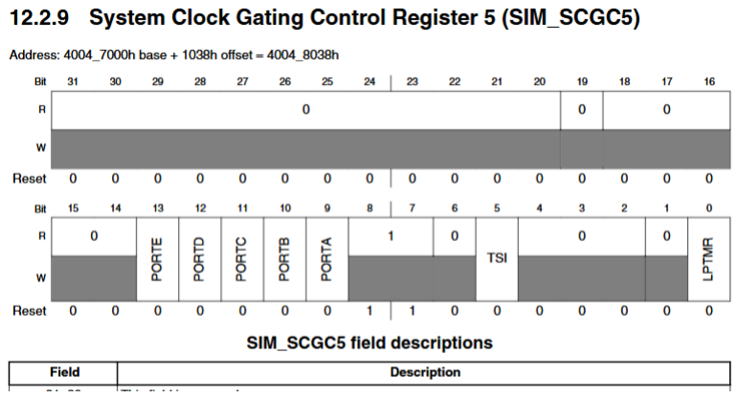
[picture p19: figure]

T. Grandpierre © / ESIEE | 25

Dans le cas du port B c’est donc le bit numéro 10 qu’il faut mettre à 1. On peut le faire très simplement avec la ligne suivante, si l’on a préalablement remarqué qu’il existait un symbole tout prêt dans le fichier MKL25Z4.h : #define SIM_SCGC5_PORTB_MASK 0x400u

On peut donc écrire :

SIM_SCGC5 |= SIM_SCGC5_PORTB_MASK;

Finalement, le programme complet devient :

#include "derivative.h" /* include peripheral declarations */

int main(void)
{
SIM_SCGC5 |= SIM_SCGC5_PORTB_MASK; //on active le PORT B
PORTB_PCR18 = (PORT_PCR_MUX(1) | PORT_PCR_DSE_MASK); //broche 53 configuré
sur bit 18 du PORT B avec DSE_MASK pour que la broche puisse sortir plus de courant
GPIOB_PDDR = (1<<18); //bit 18 du PORT B en sortie
for(;;) // boucle infinie
{
GPIOB_PTOR = (1<<18);
}

}

On le télécharge et on lance l’exécution….

Arg, la led rouge reste annulée, mais pourquoi ?

T. Grandpierre © / ESIEE | 26

En fait elle clignote tellement vite que notre œil ne s’en aperçoit pas. Il faut ajouter une boucle d’attente dans la boucle infinie afin de la ralentir :

#include "derivative.h" /* include peripheral declarations */

int main(void)
{ | int | time;
SIM_SCGC5 |= SIM_SCGC5_PORTB_MASK; //on active le PORT B
PORTB_PCR18 = (PORT_PCR_MUX(1) | PORT_PCR_DSE_MASK); //broche 53 configuré
sur bit 18 du PORT B avec DSE_MASK pour que la broche puisse sortir plus de courant
GPIOB_PDDR = (1<<18); //bit 18 du PORT B en sortie
for(;;) // boucle infinie
| {
| | GPIOB_PTOR = (1<<18);
time | = 100000;
| | while (time>=0)
time--; //pour perdre du temps
| }
}

T. Grandpierre © / ESIEE | 27

## Prise en main de la voiture

### Environnement matériel

Il faut enficher la carte de puissance au-dessus de la carte de développement FRDM-KL25Z.

Ensuite il faut connecter les moteurs de propulsions, la batterie, le servo et la caméra comme indiqué sur la figure ci-dessous :

Figure 17 – Connexions de la carte de puissance

### Programme d’exemple NxP

NxP fournit un programme complet d’exemple (« FRDM-TFC-R1.0 »)qui permet de prendre en main la carte microcontroleur ainsi que la caméra, les moteurs et le servo. Ce programme est uniquement compatible avec la carte FRDM-KL25Z connectée à la carte fille de puissance rev. 1.

Lien : https://community.nxp.com/docs/DOC-93914 , section « Codewarrior « Bare Metal Example Code »

Pour essayer ce programme :

a) Brancher votre carte en USB (il faudra peut-être rechercher les drivers manuellement dans le répertoire de freescale/CW si windows ne les trouve pas, chez moi c'est c:/Freescale/CW MCUV10.5/Drivers/Segger)
Il est important de le faire avant de lancer CW, ainsi la carte sera présente dans les menus dès le début (les profils de compilation seront existant)

T. Grandpierre © / ESIEE | 28
b) Lancer CW qui propose alors un emplacement par défaut pour le workspace : vous pouvez le changer si vous voulez, et quand vous voudrez passer d’un projet à l’autre ou l’archiver le transmettre le plus simple sera de le zipper.
c) Ensuite ouvrir un projet d’exemple existant, utilisez « Help->Welcome -> Example project » : il faut choisir le type de famille de processeur voulu (des kinetis dans notre cas) :). Attention ne pas prendre les "Processors Expert example project" pour commencer. Processor expert est très bien pour générer automatiquement des configurations de ports d'IO, de modules etc, mais n'est pas adapté quand on ne sait pas ce que l'on fait.
d) Une liste de projets pour Kinetis va alors s'afficher. Je vous conseille d'en choisir un seul à la fois. Pour savoir lequel est adapté à votre carte, élargissez la fenêtre de façon à voir le nom complet du projet exemple ainsi que son emplacement : en fonction de son emplacement (/k60 /k60 etc.) vous saurez pour quel processeur est destiné l'exemple. En cochant une case CW propose alors de copier les fichiers dans le workspace ou non, il me semble qu’une seule des 2 options fonctionne bien (il est toujours préférable de copier et laisser ainsi les fichiers originaux intacts.
e) Une fois le projet ouvert, vous avez 2 choix :
a. Soit on téléchargera le code en RAM (le programme sera perdu dès un reset ou une coupure d’alimentation)
b. Soit on téléchargera le code en mémoire Flash : c’est plus long mais le programme reste en mémoire ensuite.

Pour changer entre Flash ou RAM il suffit de cliquer sur le nom du projet (partie de gauche de CW : explorateur de fichier) et de sélectionner le mode voulu dans la liste déroulante. Parfois il n'y aura pas de choix, une seule des deux configurations aura été prévue.

f) Ensuite il suffit de compiler (build, le petit icone d'un marteau) le programme, puis de le télécharger sur la cible (download/debug, l'icône du petit insecte "bug"). Il est très important d’avoir branché la carte avant, sinon CW demande de créer soit même un profil de download/debug ce qui est fastidieux. Si il faut choisir, sur les FRDM par exemple, on utilise OpenSDA. Si aucune carte n'est trouvé, ou bien que le driver n'a pas été installé on tombe sur une fenêtre "P&E Assistant" : il faut alors essayer Refresh/Retry jusqu'à voir la carte, éventuellement changer la carte de port USB…
g) Une fois le programme télécharger, faire « run » dans le debuggeur et admirez vos leds clignoter (si c’est l’exemple que vous avez choisi) !

Autres exemples : il se peut que vous trouviez des exemples de code directement sous forme de zip sur le site de freescale ou ailleurs. Si ce sont des projets CW il faut les ouvrir en faisant "File" puis "Import" puis "Existing Projects into Workspace"

T. Grandpierre © / ESIEE | 29

### Utilisation du programme d’exemple

Sur la carte fille de puissance fournit par NxP, il y a 4 microswitchs, 4 leds et 2 potentiomètres :

Figure 18 - Dip switch, leds de la carte de puissance

Le programme d’exemple permet de tester un à un les différents éléments de la voiture en fonction de la configuration des DIP switch : (remarque connecter la batterie pour faire ces tests)

Figure 19 - DIP switch configuré à 0000

- Position 0000 : (tout sur OFF) permet de tester les 2 poussoirs (points rouges sur la photo ci-dessus) et d’allumer les leds en fonction du poussoir appuyé.
- Position 0010 : (OFF OFF ON OFF) permet de tester le servo moteur de direction. La direction tourne en fonction de la position du potentiomètre. Remarque : il est possible de connecter un 2nd servomoteur de direction et de le piloter avec le 2nd potentiomètre
- Position 0100 : permet de tester les moteurs de propulsion individuellement. La vitesse et le sens de rotation dépendent de la position des potentiomètres.
- Position 0110 : appelé aussi « Garage Mode », les valeurs correspondants à la luminosités de chacun des 128 pixels de la caméra seront envoyé sur le port série du PC au moyen du câble USB connecté entre la carte FRDM-KL25Z et le PC. Pour visualiser ces valeurs il faut :
a. Identifier sur quel port série (COM sous windows) apparait la carte KL25Z. Pour cela lancer le « gestionnaire de périphériques » windows et regarder dans « Ports(COM et LPT) » le numéro du port COM qui a été attribué à cette liaison (attention, cela peut

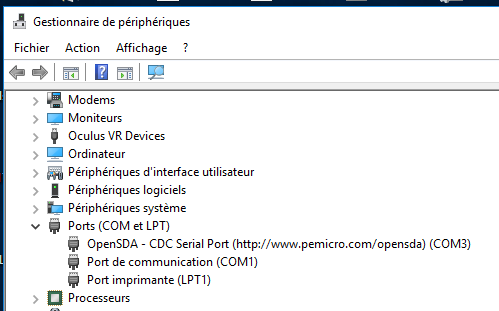
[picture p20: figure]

T. Grandpierre © / ESIEE | 30

changer entre deux connexions…). C’est par exemple COM3 sur la capture ci-dessous :

Figure 20 - Gestionnaire de périphérique où la carte apparait sur le COM3

b. Lancer un émulateur de terminal série (hyperterminal, putty, teraterm par exemple) et configurer cet émulateur pour qu’il communique avec le port COM identifié précédemment. Il faut aussi fixer la vitesse de transmission à 115200 (comme indiqué dans le fichier TFC_Config.h).

Figure 21-Configuration TeraTerm : modifier le Baudrate et le port COM

c. Une fois lancé, l’émulateur affiche à l’écran tout les octets reçus sur le port série et le code ASCII des caractères frappés au clavier sont envoyés sur ce même port série (donc vers la carte KL25Z). On doit donc voir à l’écran s’afficher des lignes de 128 nombres compris entre 0 et 4096 correspondant à l’intensité lumineuse de chacun des 128 pixels de la caméra linéaire

T. Grandpierre © / ESIEE | 31

Remarque : en fait il est possible de connecter 2 caméras linéaires, il y a donc à chaque fois affichage de 2 lignes.

En mode « garage », plutôt que d’afficher les pixels que voit la caméra sous forme numérique, il est aussi possible de les afficher graphiquement à l’aide d’un programme pour Labview (fourni dans le même zip que l’exemple TFC) ou pour Matlab ( téléchargeable sur le lien suivant : https://www.mathworks.com/matlabcentral/fileexchange/46997-nxp-cup-companion ).

Une troisième possibilité pour afficher l’image de la caméra est d’utiliser le programme que j’ai créé spécifiquement à base du framework « processing », voir annexe 1.

T. Grandpierre © / ESIEE | 32

## Description du programme d’exemple en C

### Pré-requis

Le projet contient plusieurs sous répertoires et fichiers.

- Le sous-répertoire « Sources » contient le fichier main.c c'est-à-dire le programme principal. Il contient aussi un sous-répertoire TFC : chaque fichier du programme TFC contient des fonctions spécifiques à une fonctionnalité données. C’est donc dans ce répertoire que l’on trouve le code des fonctions qui permettent de lire l’image de la caméra, de piloter les moteurs, de piloter les servos etc.
- Le sous-répertoire « Project_Headers » contient
- le fichier « MKL25Z.h » regroupant les déclaration de toutes les adresses des périphériques
- un sous-répertoire TFC qui contient les signatures des différentes fonctions définis dans « Sources\TFC »

Le fichier main.c est le plus intéressant pour commencer puisque c’est notre point d’entrée

Il commence par initialiser chacun des périphériques un à un grâce à la fonction TFC_init() ;

Puis vient la boucle infinie principale (for(;;)) qui successivement :

1. Test si des caractères ont été envoyé par l’interface série (je n’ai pas encore évoqué ce mode)
2. Récupère l’état des DIPs switchs (position 0000, 0010, etc.) et en fonction des DIPs switch exécute le code correspondant

Voici une version simplifiée de ce main :

TFC_Init();
for(;;){
switch((TFC_GetDIP_Switch()>>1)&0x03)
{
default:
case 0 : //Demo mode 0 just tests the switches and LED's
case 1 : //Demo mode 1 will just move the servos with the on-board potentiometers
case 2 : //Demo Mode 2 will use the Pots to make the motors move
case 3 : //Demo Mode 3 will be in Freescale Garage Mode. It will beam data from the Camera to the Labview Application
}
}

T. Grandpierre © / ESIEE | 33

### Gestion du temps : Systick et PIT

Systick

Avant d’étudier les différents modes, commençons par analyser comment la mesure du temps est effectuée dans ce code.

Le microcontroleur KL25Z repose sur un cœur ARM Cortex M0 générique. Ces processeurs possèdent tous un timer interne « SysTick » qui peut générer une interruption (IT) à chaque « tic » du timer. La fréquence des tic est configurable et liée à la fréquence du processeur.
Remarque : chaque constructeur rajoute ensuite ses propres périphériques timer en plus du systick, ainsi nous verrons beaucoup plus tard que NxP a aussi ajouté un périphérique « PIT ».

Dans le code TFC de l’exemple NxP, on trouve la configuration de ce timer dans la fonction
« TFC_InitSystick () » appelé par TFC_Init( ) au début du main :

static volatile unsigned int DelayTimerTick = 0; volatile uint32_t TFC_Ticker[NUM_TFC_TICKERS];

void TFC_InitSysTick()
{
uint8_t i;

for(i=0;i<NUM_TFC_TICKERS;i++) TFC_Ticker[i] = 0;

SYST_RVR = CORE_CLOCK/SYSTICK_FREQUENCY;
SYST_CSR = | SysTick_CSR_ENABLE_MASK | | SysTick_CSR_TICKINT_MASK |
SysTick_CSR_CLKSOURCE_MASK;
//Important! | Since the Systick is part of the Cortex core and NOT a
kinetis peripheral its Interrupt line is not passed through NVIC. | You
need to make sure that the SysTickIRQ function is poopulated in the vector table. See the kinetis_sysinit.c file
}
Elle :
1. initialise un tableau de 4 entiers sur 32 bits déclarés dans le même fichier (le tableau étant déclaré en dehors du main il est donc global et accessible à toutes les fonctions)
2. indique la fréquence du quartz utilisé pour cadencer le processeur (48 Mhz ici )
3. autorise les interruptions timer : quand une interruption Systick surviendra, le processeur cherchera dans sa table de vecteur d’interruption l’adresse de la fonction d’interruption associée. Cette table est configurée dans le fichier kinetis_sysinit.c du répertoire /Project_Settings/Startup_Code. On y découvre que la fonction qui sera appelée s’intitule « SysTick_Handler »
4. void SysTick_Handler()

T. Grandpierre © / ESIEE | 34
5. {
6. uint8_t i;
7.
8. if(DelayTimerTick<0xFFFFFFFF)
9. {
10. DelayTimerTick++;
11. }
12.
13. for(i=0;i<NUM_TFC_TICKERS;i++)
14. if(TFC_Ticker[i]<0xFFFFFFFF)
15. TFC_Ticker[i]++;
16. }

A chaque interruption (donc chaque milleseconde), la variable globale « DelayTimerTick » qui sert de compteur est incrémentée sauf si la valeur maximum du compteur est atteinte.
De cette façon, grâce à la fonction suivante, il est possible de compter le temps :

void TFC_Delay_mS(unsigned int TicksIn_mS)
{
DelayTimerTick = 0;

while(DelayTimerTick<TicksIn_mS) {
}
}

En plus de cela, les 4 éléments du tableau TFC_Ticker sont aussi incrémentés à chaque tick ce qui permet de disposer de 4 compteurs individuels supplémentaires de temps que l’on pourra utiliser plus tard dans les fonctions.

PIT

Le PIT (Periodoc Interrupt Timer) est un périphérique timer spécifique de la famille Kinetis de NxP. Il n’est pas capable de piloter des broches du processeurs, mais en revanche il peut piloter des périphériques interne et générer des interruptions. Nous verrons par exemple qu’il sera utilisé pour déclencher périodiquement les mesures de tension electrique (batterie, potentiomètres et caméra) mais aussi pour régler le temps d’exposition de la caméra.

Pour des raisons que nous verrons plus tard (mode 1), le PIT est initialisé (en rouge) dans la fonction qui initialise l’ADC :

void TFC_InitADCs()
{

InitADC0();

T. Grandpierre © / ESIEE | 35

//All Adc processing of the Pots and linescan will be done in the ADC0 IRQ!
//A state machine will scan through the channels.
//This is done to automate the linescan capture on Channel 0 to ensure that timing is very even
CurrentADC_State = | ADC_STATE_INIT;
//The pump will be primed with the PIT interrupt. | upon
timeout/interrupt it will set the SI signal high
//for the camera and then start the conversions for the pots.

//Enable clock to the PIT
SIM_SCGC6 |= SIM_SCGC6_PIT_MASK;

//We will use PIT0
TFC_SetLineScanExposureTime(TFC_DEFAULT_LINESCAN_EXPOSURE_TIME_uS); //enable PIT0 and its interrupt
PIT_TCTRL0 = PIT_TCTRL_TEN_MASK | PIT_TCTRL_TIE_MASK;

PIT_MCR |= PIT_MCR_FRZ_MASK; // stop the pit when in debug mode //Enable the PIT module
PIT_MCR &= ~PIT_MCR_MDIS_MASK;

enable_irq(INT_PIT-16);
enable_irq(INT_ADC0-16);

}
Avec la fonction qui configure simplement la période des interruptions générées par le PIT :
void | TFC_SetLineScanExposureTime(uint32_t | TimeIn_uS)
{
float t;
//Figure out how many Pit ticks we need for for the exposure time t = (TimeIn_uS /1000000.0) * (float)(PERIPHERAL_BUS_CLOCK);
| PIT_LDVAL0 = (uint32_t)t;

}

Ensuite la fonction PIT_IRQHandler() est exécuté à chaque interruption de ce timer :

### Etude du Mode 0 : test des switchs et leds

Rappelons que dans ce mode, les leds reflètent l’état des switchs et DIP switch.

case 0 :
//Demo mode 0 just tests the switches and LED's if(TFC_PUSH_BUTTON_0_PRESSED)
TFC_BAT_LED0_ON;
else
TFC_BAT_LED0_OFF;

T. Grandpierre © / ESIEE | 36

if(TFC_PUSH_BUTTON_1_PRESSED) TFC_BAT_LED3_ON;
else
TFC_BAT_LED3_OFF;

if(TFC_GetDIP_Switch()&0x01) TFC_BAT_LED1_ON;
else
TFC_BAT_LED1_OFF;

if(TFC_GetDIP_Switch()&0x08) TFC_BAT_LED2_ON;
else
TFC_BAT_LED2_OFF;

break;

TFC_PUSH_BUTTON_0_PRESSED : ce n’est pas une fonction mais une macro ! Il faut donc chercher sa défintion. On verra qu’elle interroge le matériel pour connaitre l’état du bouton poussoir. Cette macro est codée dans le fichier TFC-BoardSupport .h

#define TFC_PUSH_BUTTON_0_PRESSED ((GPIOC_PDIR&TFC_PUSH_BUTT0N0_LOC)>0)

Lors de la compilation cette macro sera donc remplacée par : (GPIOC_PDIR&TFC_PUSH_BUTT0N0_LOC)>0

Pour comprendre cette ligne, il faut :
- Le schéma de la carte fille où apparait le bouton poussoir : FRDM-TFC_Schematics.pdf
- Le schéma de la carte FRDK-KL25Z pour savoir sur quelle broche est connecté le bouton poussoir : FRDM-KL25Z_SCH_REV_E.pdf
- La datasheet du processeur pour connaitre le rôle de cette broche et le périphérique associé : KL25P80M48SF0.pdf
- Le référence manuel du processeur KL25Z pour savoir comment accéder à l’état de cette broche (liste des registres à configurer etc.) : KL25P80M48SF0RM.pdf

Jeu de piste :

1. On part du schéma de la carte fille de puissance (page 1 de : FRDM-TFC_Schematics.pdf)
2. On cherche le bouton poussoir. Il est nommé SW1.

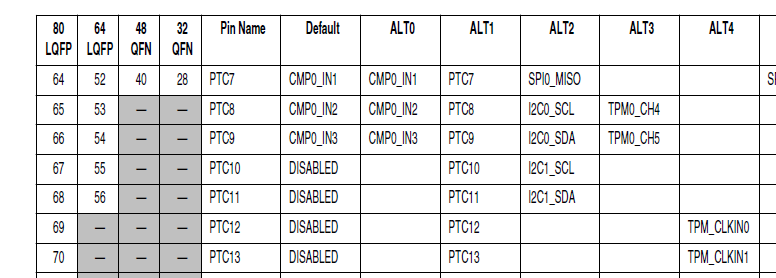
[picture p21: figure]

T. Grandpierre © / ESIEE | 37
3. On découvre qu’il est connecté au fil nommé PTC13.
4. On retrouve ce fil sur la broche 3 du connecteur J2 de la carte de puissance.
5. Quand cette carte est enfichée sur la carte KL25Z on découvre (p5 de FRDM-KL25Z_SCH_REV_E.pdf ) que ce fil conserve le même nom (merci aux ingénieurs NxP qui sont très rigoureux !) et conduit à la broche numéro 70 de nom
« PTC13/TPM_CLKIN1 ».
6. En cherchant cette broche sur la data sheet page du processeur, on découvre (p48 de KL25P80M48SF0.pdf et dans la colonne « 80 LQFP » puisque c’est le suffixe de la référence de notre processeur soudé sur cette carte, cela correspond au nombres de broches) que cette broche peut être configurée pour l’une des deux fonctions : PTC13 (colonne ALT1) ou TPM_CLKIN1 (colonne ALT 4), bien sûr on aurait pu s’en douter d’après le nom donné sur cette broche, mais croyez-moi il est toujours préférable de vérifier !!).
7. En effet, en lisant le référence manuel (KL25P80M48SF0RM.pdf ) et en particulier le chapitre 11 « Port control and interrupts) , on découvre qu’il est possible de choisir le périphérique auquel on veut connecter la broche en fonction de la valeur « ALT » qu’il faut placer dans les bits 10 à 8 du registre « Pin Control Register n »,
communément appelé « PORTx_PCRn » (p184).

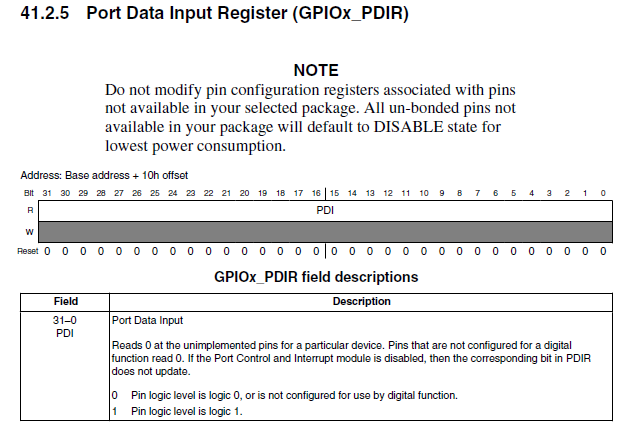
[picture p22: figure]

T. Grandpierre © / ESIEE | 38
8. Toujours d’après le référence manuel, on découvre que PTC13 correspond au rôle de broche d’entrée-sortie à usage générale : GPIO. Les broches sont regroupées par paquets de 16, pour former des ports : port A, port B, port C etc. (le nombre de port dépend du microcontrôleur, de son boitier etc.).
9. Le switch SW1 est donc connecté au port C, bit n°13 !

Pour connaitre l’état du switch il faut donc lire l’état du registre GPIO associé à cette broche. C’est très simple sur cette famille de processeur car en lisant le registre « Port Data Input Register » (p 777), appelé communément « GPIOx_PDIR) on obtient l’état de chaque bit du port correspondant.

Dans notre cas, puisque SW1 est sur la broche 13 du port C il suffit de lire le bit n°13 (à l’aide d’un masque) le registre GPIOC_PDIR :

En écrivant donc a=GPIOC_PDIR& (1<<13) ; la valeur de a sera l’état du switch.

Comme on évite de coder des valeurs en « dur », les ingénieurs qui ont conçu ce code, ont déclaré dans un fichier spécifique à la carte (TFC_BoardSupport.c), la position de ce bit grâce à la ligne

#define TFC_PUSH_BUTT0N0_LOC | ((uint32_t)(1<<13))

Maintenant on peut donc comprendre toute la ligne :

T. Grandpierre © / ESIEE | 39
#define TFC_PUSH_BUTTON_0_PRESSED | ((GPIOC_PDIR&TFC_PUSH_BUTT0N0_LOC)>0)

Oui mais….ceci fonctionne car la broche PTC13 à correctement été initialisée en entrée et pour le mode ALT1. Ceci a en effet été effectué dans la fonction « void TFC_Init()” qui appelle la

fonction TFC_InitGPIO();

Dans cette fonction on retrouve en effet les lignes suivante : «PORTC_PCR13 = PORT_PCR_MUX(1); » Avec :
#define PORTC_PCR13 | PORT_PCR_REG(PORTC_BASE_PTR,13)

#define PORT_PCR_MUX(x)

(((uint32_t)(((uint32_t)(x))<<PORT_PCR_MUX_SHIFT))&PORT_PCR_MUX_MASK

Notons que par défaut les broches d’un port sont configurées en entrées après un reset (page 778, section 41.2.6) , donc rien à effectuer ici.

La suite du code du mode 0 repose sur le même principe. Il suffit de regarder sur les schémas où sont connectés les DIPs switchs, les leds.

Notons cependant que pour les leds il faut configurer les broches en sortie à l’aide du registre GPIOn_PDDR, avec n=B puisque les leds sont sur les bits 8 à 11 du port B., d’où la ligne suivante
GPIOB_PDDR = TFC_BAT_LED0_LOC | TFC_BAT_LED1_LOC | TFC_BAT_LED2_LOC |
TFC_BAT_LED3_LOC;

Leds sur le schema de la carte fille :

Connection des leds aux processeur

T. Grandpierre © / ESIEE | 40

Configuration des multiplexeur pour commander les leds en mode GPIO :

D’où les lignes de configuration

//Ports for LEDs
PORTB_PCR8 = PORT_PCR_MUX(1) | | PORT_PCR_DSE_MASK;
PORTB_PCR9 = PORT_PCR_MUX(1) | | PORT_PCR_DSE_MASK;
PORTB_PCR10 = PORT_PCR_MUX(1) | | PORT_PCR_DSE_MASK;
PORTB_PCR11 = PORT_PCR_MUX(1) | | PORT_PCR_DSE_MASK;

### Mode 1 : test du servomoteur de direction

Rappelons que ce mode permet de tester les servomoteurs grâce aux potentiomètres.

Voici le code :

case 1:
//Demo mode 1 will just move the servos with the on-board potentiometers if(TFC_Ticker[0]>=20)
{
TFC_Ticker[0] = 0; //reset the Ticker //Every 20 mSeconds, update the Servos TFC_SetServo(0,TFC_ReadPot(0)); TFC_SetServo(1,TFC_ReadPot(1));
}

//Let's put a pattern on the LEDs if(TFC_Ticker[1] >= 125)
{
TFC_Ticker[1] = 0;
t++;
if(t>4)

T. Grandpierre © / ESIEE | 41

{
t=0;
}
TFC_SetBatteryLED_Level(t);
}

TFC_SetMotorPWM(0,0); //Make sure motors are off TFC_HBRIDGE_DISABLE;

break;

Il contient deux parties :

Une partie qui lit l’état des potentiomètres grâce à la fonction ReadPot(x) où x = 0 ou 1 en fonction du potentiomètre à lire, puis applique la valeur de consigne lue au servo-moteur grâce à la fonction TFC_SetServo dont le premier argument est le numéro de servo (on en utilise qu’un, le 0) et le second argument la valeur de position à appliquer au servo.

Une partie qui affiche un chenillard sur les 4 leds. Cela s’effectue à l’aide d’une boucle et d’un compteur t. Cette partie utilise la fonction TFC_SetBatteryLED_Level(x) où x est le numéro de la led à allumer.

On remarque que dans ce mode les moteurs de propulsion sont désactivés (voir explication mode suivant).

Notons que ce code utilise intensivement le tableau de compteur de temps
« TFC_Ticker[4] ». Grâce à la ligne TFC_Ticker[0] = 0; on remet le compteur 0 à zéro, puis on attend que 20 ms se soient écoulées pour recommencer : if(TFC_Ticker[0]>=20)…
Pour le chenillard à led, c’est un deuxieme compteur de temps TFC_Ticker[1] qui est utilisé.

Configuration de l’ADC

Dans ce mode la valeur des potentiomètres est lue grâce à l’ADC (Analog to Digital Converter), mais il est aussi périodiquement utilisé pour :

- Lire l’état de la batterie
- Lire la position des 2 potentiomètres
- Lire les 128 pixels des 2 caméras linéaires.

Pout cela le PIT (périphérique Timer) génère une interruption (IT) périodiquement. Chaque interruption déclenche le démarrage d’une conversion ADC (lecture de la tension du potentiomètre 0).

Quand l’ADC a fini la conversion, il génère une IT de fin de conversion qui démarre une nouvelle conversion sur une autre entrée de l’ADC. Le changement d’entrée et le lancement de la conversion se font grâce à une machine à état codée dans l’interruption de fin de conversion ADC.

T. Grandpierre © / ESIEE | 42

Voici le code de la fonction d’initialisation de l’ADC « TFC_InitADCs() »

void TFC_InitADCs()

{

InitADC0();

//All Adc processing of the Pots and linescan will be done in the ADC0 IRQ!

//A state machine will scan through the channels.

//This is done to automate the linescan capture on Channel 0 to ensure that timing is very even

T. Grandpierre © / ESIEE | 43

CurrentADC_State =ADC_STATE_INIT;

//The pump will be primed with the PIT interrupt. upon timeout/interrupt it will set the SI signal high

//for the camera and then start the conversions for the pots.

//Enable clock to the PIT

SIM_SCGC6 |= SIM_SCGC6_PIT_MASK;

//We will use PIT0

TFC_SetLineScanExposureTime(TFC_DEFAULT_LINESCAN_EXPOSURE_TIME_ uS);

//enable PIT0 and its interrupt

PIT_TCTRL0 = PIT_TCTRL_TEN_MASK | PIT_TCTRL_TIE_MASK;

PIT_MCR |= PIT_MCR_FRZ_MASK; // stop the pit when in debug mode

//Enable the PIT module

PIT_MCR &= ~PIT_MCR_MDIS_MASK;

enable_irq(INT_PIT-16);

enable_irq(INT_ADC0-16);

}

Et une partie de la machine à état codée dans l’interruption ADC :

#define ADC_STATE_INIT | 0

#define ADC_STATE_CAPTURE_POT_0 | 1

#define ADC_STATE_CAPTURE_POT_1 | 2

#define ADC_STATE_CAPTURE_BATTERY_LEVEL3 #define ADC_STATE_CAPTURE_LINE_SCAN 4 void ADC0_IRQHandler() {

uint8_t Junk;
switch(CurrentADC_State) {
default: Junk = ADC0_RA; break
case ADC_STATE_CAPTURE_POT_0:
PotADC_Value[0] = ADC0_RA;
ADC0_CFG2 &= ~ADC_CFG2_MUXSEL_MASK; //Select the A side of the mux
ADC0_SC1A = TFC_POT_1_ADC_CHANNEL | ADC_SC1_AIEN_MASK;
CurrentADC_State = ADC_STATE_CAPTURE_POT_1;

T. Grandpierre © / ESIEE | 44

break;
case ADC_STATE_CAPTURE_POT_1:
PotADC_Value[1] = ADC0_RA;
ADC0_CFG2 |= ADC_CFG2_MUXSEL_MASK; //Select the B side of the mux ADC0_SC1A = TFC_BAT_SENSE_CHANNEL| ADC_SC1_AIEN_MASK; CurrentADC_State = ADC_STATE_CAPTURE_BATTERY_LEVEL;
break;
case ADC_STATE_CAPTURE_BATTERY_LEVEL:

……/……

### Mode 2 : test des moteurs de propulsion

Rappelons que ce mode permet de tester les 2 moteurs de propulsions à l’aide de la position des 2 potentiomètres.

Voici le code correspondant :

case 2 :

//Demo Mode 2 will use the Pots to make the motors move
TFC_HBRIDGE_ENABLE;
TFC_SetMotorPWM(TFC_ReadPot(0),TFC_ReadPot(1));

//Let's put a pattern on the LEDs if(TFC_Ticker[1] >= 125)
{
TFC_Ticker[1] = 0;
t++;
if(t>4)
{
t=0;
}
TFC_SetBatteryLED_Level(t); }
break;

Comme pour le mode 1, la fonction TFC_ReadPot (x) permet de lire la tension des potentiomètres, et applique cette valeur aux moteurs grâce à la fonction TFC_SetMotorPWM qui reçoit 2 arguments signés correspondants aux consignes de vitesse des 2 moteurs.

En parallèle, comme pour le mode 1, ce code affiche un chenillard sur les 4 leds de batterie.

### Mode 3 : test des caméras (mode garage)

case 3 :

T. Grandpierre © / ESIEE | 45
//Demo Mode 3 will be in Freescale Garage Mode. | It will beam data from the
Camera to the Labview Application

if(TFC_Ticker[0]>100 && LineScanImageReady==1)
{
TFC_Ticker[0] = 0;
LineScanImageReady=0;
TERMINAL_PRINTF("L:");
if(t==0)
t=3;
else
t--;
TFC_SetBatteryLED_Level(t);

for(i=0;i<128;i++)
{
TERMINAL_PRINTF("%d ",LineScanImage0[i]); }

../..

break;

}

On attend que 100 ms soient écoulées (TFC_Ticker[0]>100) et qu’une image ait été

acquise et disponible dans le buffer d’image (LineScanImageReady==1)

Si c’est le cas : on rafraîchit la position du chenillard de led (code en bleu), et on récupère la valeur de chacun des 128 pixels de l’image et on l’envoie sur le port série vers le PC grâce à la macro TERMINAL_PRINTF.

L’information à retenir : la valeur des pixels de l’image est stockée dans le tableau « LineScanImage0[ ] » . Notons que ce code affiche les pixels d’une seconde caméra qui pourrait être connectée à côté de la première et dont les pixels seraient stockés dans « LineScanImage1[ ] » .

T. Grandpierre © / ESIEE | 46

## Travail à effectuer

A partir des fonctions étudiées précédemment, il s’agit maintenant de coder l’application de suivi de piste. Cette application doit comporter plusieurs parties :

- Détection des bandes noires latérales
- Calcul de la position de la voiture par rapport aux bandes
- Calcul de consignes à appliquer au servo de direction (pour être parallèle aux lignes)
- Calcul de la consigne de tension à appliquer aux moteurs de propulsion (fonction de la trajectoire, ralentir dans les virages pour ne pas sortir)
- Détection de la fin du parcours.

La vitesse de propulsion est initialement pilotée à l’aide de la valeur de PWM appliquée au moteur. Hors la tension qui va être commutée par PWM n’est pas constante, elle dépend de l’état des batteries, il n’y a donc pas actuellement de consigne en vitesse précise. Le premier objectif est donc d’ajouter un asservissement en vitesse avant de travailler sur l’asservissement en position de la voiture.

D’autres éléments seront à ajouter pour les phases de tests : capteur d’obstacle ultrasons ou bumper à l’avant pour arrêter la voiture face à un mur. Ajout de module radio.

### Asservissement en vitesse : implémentation

Il faut :

- Mesurer la vitesse de la voiture
- Calculer la différence entre la vitesse souhaitée et la vitesse voulue
- Transformer cette valeur en consigne PWM ( multiplication par un coefficient, implémentation éventuelle d’un PID)
- Appliquer ce résultat aux moteurs

Voici une représentation graphique de cette asservissement. Sur ce schéma la première boite
« Calcul de la consigne de vitesse de la voiture » est fonction de la position de la voiture i.e. est-elle dans un virage, une ligne droite etc.

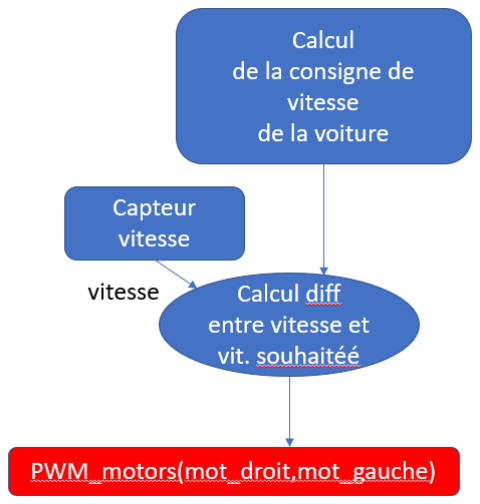
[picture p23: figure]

T. Grandpierre © / ESIEE | 47

Pour mesurer la vitesse il existe plusieurs solutions. Nous avons retenu le principe de compter le nombre de tours de roues en un temps fixe donné. Pour cela il faut ajouter un capteur de rotation sur l’une ou les deux roues.

Puisque le règlement impose des capteurs NxP, nous avons utilisé le capteur KMI16/1 « Rotational Sensor » qui est capable de detecter les variations du champ magnétique qu’il génère grâce à un aimant solidaire de son boitier. Nous avons donc fixé une dizaine de petites vis métalliques sur une bague en PLA (fabriquée par imprimante 3D) et fixée autour de l’une des roues de la voiture.

Figure 22 - Bague en PLA noir avec les vis métalliques (à gauche) et capteur KMI16 (à droite)

Le capteur KMI17 génère une impulsion électrique chaque fois qu’une des vis passe devant le capteur.

T. Grandpierre © / ESIEE | 48

Figure 23-KMI16 Sensor –(Source NxP)

Ce capteur est très facile à interfacer comme le montre le schéma suivant tiré de la note d’application. Nous l’avons utilisé exactement comme préconisé :

Remarque : les moteurs génèrent beaucoup de parasites qui peuvent perturber le comptage, pour les absorber il est important de câbler des condensateurs au plus près des bornes de chaque moteur

Pour convertir ces impulsions en vitesse de rotation il faut en permanence compter le nombre d’impulsion pendant un temps connu. Pour cela, plusieurs techniques logicielles :

- Utiliser le processeur pour faire du polling, c'est-à-dire tester en permanence l’état de la broche d’entrée connectée au capteur : c’est très consommateur de temps CPU puisque le CPU ne peut rien faire d’autre, et on risque de manquer des impulsions si la boucle ne s’exécute pas assez vite.
- Utiliser une interruption matérielle : chaque impulsion sur la broche d’entrée connectée au capteur génère une impulsion. Le processeur exécute le programme d’interruption correspondant à chaque fois que le niveau passe à l’état haut (par exemple). Dans le programme d’interruption on incrémente un compteur puis on quitte l’interruption, le processeur peut ainsi poursuivre l’exécution du travail en cours. Ceci à l’avantage de décharger partiellement le processeur qui peut faire autre chose i.e. il n’est plus monopolisé. Cependant, les interruptions seront très nombreuses ce qui fait perdre beaucoup de temps.
- Utiliser un périphérique dédié du processeur, capable de compter des évènements extérieurs. En général par le biais d’un timer dont l’horloge est le signal du capteur. Chaque constructeur propose une ou plusieurs solutions pour ce problème de comptage assez

T. Grandpierre © / ESIEE | 49

classique. Cette solution est la meilleure puisque le processeur n’a plus qu’à interroger périodiquement ou sporadiquement ce périphérique pour connaitre le nombre d’impulsion survenue. Aucun temps processeurs n’est donc gaspillé à compter.

Sur la famille Kinetis, nous avons choisi d’utiliser le périphérique DMA pour réaliser cette tâche. C’est assez inhabituel d’utiliser ce périphérique habituellement dédié à transférer des blocs de données entre 2 espaces mémoires.

En effet un DMA (Direct Memory Access) est conçu pour transférer un bloc de données d’une zone mémoire à une autre, sans intervention du processeur. Il peut même effectuer plusieurs transferts simultanément grâce à plusieurs canaux.

Pour simplifier, la configuration d’un transfert par un canal DMA consiste à programmer quelques registres :

- Un registre où l’on indique l’adresse de base de la zone à transférer
- Un registre où l’on indique l’adresse de destination
- Un registre où l’on indique le nombre d’éléments à copier
- Un registre de configuration du canal DMA.

Parmi les configurations possibles on peut choisir de synchroniser chaque transfert élémentaire avec un évènement interne ou externe. C’est cette dernière possibilité que l’on va choisir.

Ainsi, on va configurer le DMA comme si l’on voulait effectuer le transfert d’un bloc de données, vers une autre zone de donnée en indiquant un très grand nombre d’élément. Puis dans les options on va configurer le DMA pour que chaque transfert soit synchronisé avec le changement d’état de la broche sur laquelle sera connecté le capteur.

A chaque impulsion, le compteur du DMA est donc incrémenté. Il suffit ensuite de lire périodiquement le compteur du DMA pour connaitre le nombre de tour de roues effectués par la voiture, et de remettre le compteur à zéro.

La lecture et la remise à zéro du compteur peuvent se faire dans une interruption exécutée périodiquement, afin d’avoir une mesure de la vitesse précise en permanence.

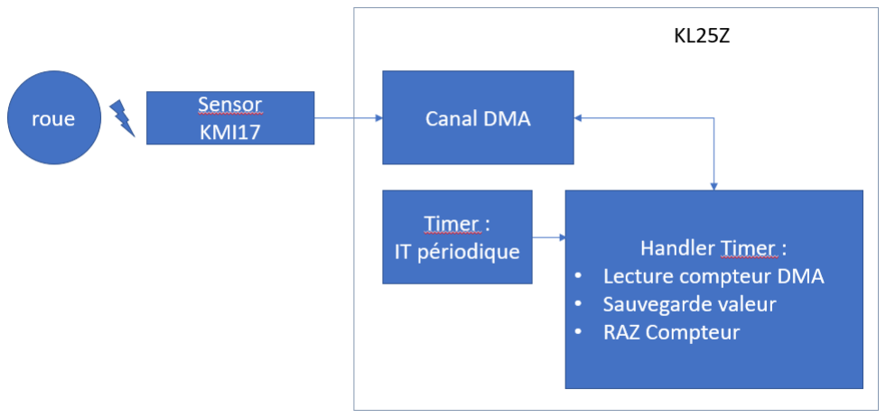
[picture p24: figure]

T. Grandpierre © / ESIEE | 50

### Asservissement position : implémentation

Temps d’exposition

Nous avons vu que la démo NxP fournit une fonction qui retourne le contenu de la caméra sous la forme d’un tableau de 128 pixels dont l’intensité lumineuse est comprise en 0 et 4096 (utilisation d’un ADC configuré en mode 12 bits). Le 0 correspond à la couleur noir, 4096 au blanc. Toutes les valeurs intermédiaires correspondent à des niveaux de gris entre le blanc et le noir.

Bien sûr, ceci est fonction de l’éclairement, et donc tu temps d’exposition de la caméra. Pour simplifier l’explication, on peut dire que chaque pixel du capteur est un constitué d’un capteur qui « compte » le nombre de photon qui arrivent pendant le temps qu’on appelle « d’exposition ».

Dans cette implémentation, le temps d’exposition correspond au temps qui s’écoule entre deux lectures du capteur : plus on fixe un temps d’exposition élevé, plus on laisse de temps aux photons d’arriver sur le capteur, plus l’image sera claire. C’est donc idéal dans le cas de zones peu éclairées pour augmenter la sensibilité. En revanche, si la scène est déjà très éclairée, les objets sombres risquent d’apparaitre très clairs, il sera donc difficile de les distinguer du fond.

Le temps d’exposition est configurable, il se fixe avec la fonction « void TFC_SetLineScanExposureTime(uint32_t TimeIn_uS) » qui reçoit un entier sur 32 bits.

T. Grandpierre © / ESIEE | 51
void TFC_SetLineScanExposureTime(uint32_t | TimeIn_uS)
{
float t;

//Figure out how many Pit ticks we need for for the exposure time
t = (TimeIn_uS /1000000.0) * (float)(PERIPHERAL_BUS_CLOCK); PIT_LDVAL0 = (uint32_t)t;

}

Comme nous l’avons vu précédemment, cette fonction configure simplement la période du PIT qui sert à déclencher l’ADC.

Le réglage de l’exposition est un élément crucial pendant la compétition où les éclairages peuvent être très différents des salles de notre école. Il est donc important de réfléchir à un algorithme de calcul d’exposition idéale et automatique permettant d’avoir l’amplitude de valeur maximale à chaque instant.

Détection des bandes noires

Il existe plusieurs techniques pour détecter les bords des objets dans une image. Nous présentons ici la plus simple basée sur la variation du gradient.

Dans l’image, nous recherchons les bords des bandes noires sur fond blanc. Comme évoqué plus haut, le fond blanc se traduit par des valeurs élevées dans le tableau de pixels alors que les bandes noires se traduisent par des valeurs faibles dans le tableau de pixels. Nous pouvons donc détecter les bords des bandes noires en calculant la variation de luminosité entre 2 pixels consécutifs. Ainsi quand nous sommes dans une zone homogène, la variation de valeur sera faible. En revanche quand nous sommes sur un bord, la variation de la valeur sera beaucoup plus forte.

Par exemple sur cette photo on distingue des valeurs élevées au centre de la courbe (i.e. bande blanche) et des valeurs faibles de chaque côtés (i.e. bandes noires) qui n’atteignent jamais 0.

T. Grandpierre © / ESIEE | 52

Il faut donc construire un deuxième tableau « gradient » dans lequel on calcul les variations de luminosité entre chaque pixel consécutif : une simple boucle qui parcourt les 128 éléments et fait la différence entre la case courante et la case suivante.

Ensuite, dans ce tableau « gradient » il suffit de rechercher les valeurs maximales puisqu’elles correspondent aux bords des bandes noires. Pour chaque valeur trouvée on conserve sont indice dans le tableau : cet indice correspond à la position physique du bord correspondant.

Remarque : ceci n’est qu’une première possibilité de détection, il en existe d’autres, ont peut par exemple utiliser l’algorithme des K plus proches voisins (K-means)

Pour calculer ensuite la consigne à donner au servo, il faut ensuite avoir décidé à quelle position on souhaite toujours maintenir la voiture du bord i.e. quelle valeur d’indice on souhaite trouver ci-dessus. Il suffit ensuite de faire la différence entre cette valeur et la valeur trouvée, de la convertir en une valeur de consigne pour le servo et l’appliquer au servo. L’utilisation d’un PID peut s’avérer indispensable pour éviter les oscillations de la voiture.

Voici le schéma récapitulatif de cette partie

T. Grandpierre © / ESIEE | 53

### Fusion des asservissements

Il s’agit ensuite de regrouper l’ensemble des asservissements développés dans une même application. Il faudra aussi ajouter une machine à état qui permet de décider de la vitesse à adopter en fonction de la trajectoire à effectuer pour ne pas sortir des virages par exemple, et accélérer au maximum dans les lignes droites.

Ci-dessous le schéma fonctionnel du travail à réaliser : la partie de droite représente l’asservissement en vitesse, la partie de gauche l’asservissement en position.

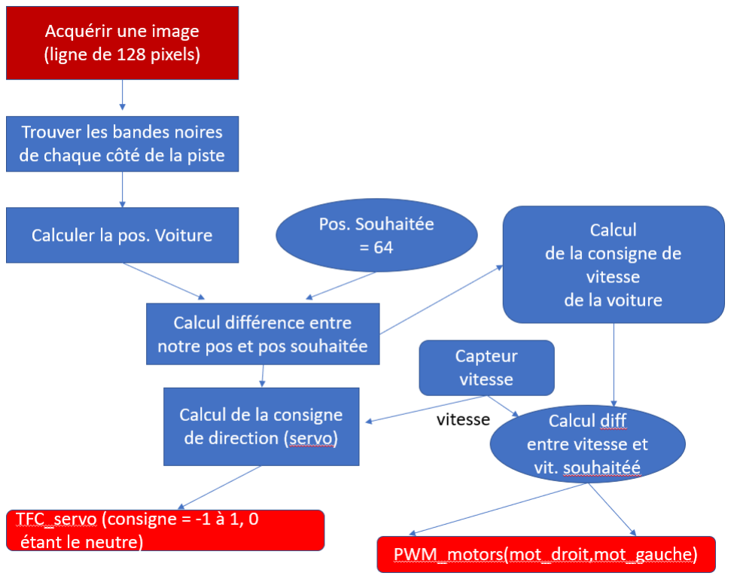
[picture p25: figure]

T. Grandpierre © / ESIEE | 54

### Détection de collision

Lors des essais, il est courant que la voiture quitte la piste et finissent bloquée contre un obstacle avec les moteurs alimentés. Ceci est très néfaste pour les engrenages en plastique du chassis Model-
C. Il est donc prudent de placer un dispositif qui arretera les moteurs dans cette situation.

Pour cela il existe plusieurs solutions :

- Pare-chocs actif : on dispose des boutons poussoirs fixés sur un pare-choc à l’avant du véhicule.
- Détecteur à ultrasons : on place un émetteur / récepteur à ultrasons pour mesurer la distance entre l’avant du véhicule et les obstacles. Si la distance devient inférieur à une certaine limite on coupe les moteurs .

T. Grandpierre © / ESIEE | 55
- Utilisation d’un LIDAR : comme les ultrasons, ce dispositif permet de mesurer une distance mais à l’aide d’un Laser.

La première solution est la plus simple à mettre en œuvre bien qu’elle ait l’inconvénient de ne pas empêcher la collision.

Pour cela il suffit de câbler un bouton poussoir sur une entrée GPIO du processeur. Puis de configurer cette broche pour qu’elle génère une interruption. Dans le handler d’interruption associé on coupera l’alimentation des moteurs.

Il faut donc d’abord configurer la broche qui sera connectée au pare-chocs :

- Identifier une broche disponible
- Configurer la broche en entrée (cas par défaut),
- Configurer le multiplexeur de cette broche en fonction de son rôle (voir tableau pour valeur du MUX)
- Autoriser cette broche à générer des interruptions (registre PORT_PCR_IRQx(n°), PORT_PCR_PE_MASK, PORT_PCR_PS_MASK
- Autoriser les interruptions du port correspondant : enable _irq (INT_PORTn-16)

Il faut ensuite écrire la fonction handler de l’interruption. Remarque : dans ce handler il faut rechercher la broche qui a généré l’interruption car il n’y a qu’une IT par PORT .

Par exemple si l’on a configuré la broche 12 du port C pour qu’elle génère une interruption :

int PortC_IRQHandler(int stop)

{

uint32_t res=0;

res = (GPIOC_PDIR) & (1<<12); // test de la broche 12 du port C

../..

}

T. Grandpierre © / ESIEE | 56

## Annexe 1 – Programme processing pour afficher l’image de la caméra linéaire

1) téléchargez et installer processing https://processing.org/
2) Modifiez la démo fourni par Freescale/NxP (programme FRDM-TFC-R1.0) qui permet de tester les moteur, le servo etc en remplacant le code qui suit (à partir de « case 3 ») par :

/********************************DEBUT****************************/

case 3 :

if(TFC_Ticker[0]>100 && LineScanImageReady==1) { TFC_Ticker[0] = 0;
LineScanImageReady=0;
//TERMINAL_PRINTF("\r\n"); TERMINAL_PRINTF("L:");
if(t==0)
t=3;
else
t--;
TFC_SetBatteryLED_Level(t);

TERMINAL_PRINTF("%d ",0);
//TERMINAL_PRINTF("%d ",255); for(i=0;i<128;i++) {
TERMINAL_PRINTF("%d
",LineScanImage0[i]);
}

}

/********************************FIN***************************/

3) Dans processing, créer un fichier : fichier -> nouveau, et copier le code ci-dessous (jusqu'en bas de la page)

Remarque : modifier le code en fonction du COM port qui est attribué par windows, dans cet exemple ma carte KL25Z était associé au port COM5 et apparaissait en 2nd dans la liste des ports COM.

/***********************DEBUT************************************/

/*
T.Grandpierre fevrier 2016 - Processing 3
Pour récupérer l'image de la camera freescale KL25Z et l'afficher sous forme oscillo + forme image
*/

T. Grandpierre © / ESIEE | 57

import processing.serial.*; // importation de la librairie de communication serie
//variables
Serial maConnection; // Crée un objet de communication série int x=0;
int y=0;
int i=0;
int[] ligne0;

void setup() {
size(650, 650); // taille de la fenetre
String NomDuPort = Serial.list()[1]; // récupère la 2nd interface serie trouvée
//car sur mon PC j'ai COM1 puis COM5 et c'est COM5 qui est associé à la KL25Z
println("connection a "+NomDuPort);
maConnection = new Serial(this, NomDuPort, 115200); // création de la connexion série
smooth(); // lisser les dessins
strokeWeight(1); // largeur de trait
stroke(40); // couleur du trait gris
ligne0 = new int[139]; //tableau de pixels qu'on va récuperer par l'interface serie
i=0; //compteur de pixels, pour le tableau de pixels background(0);
stroke(255);
}

void draw() { //boucle de dessin principale background(0); //fond noir
noFill(); //pas de remplissage des formes (rectangle) stroke(255); //ligne de couleurs blanches
//dessine forme du signal :
for (int x=0; x<128;x++) {
//ligne0[i] contient la valeur du pixel i line(x,300-ligne0[x],x+1,300-ligne0[x+1]); }
//dessine image de la caméra
for (int x=0; x<128;x++) { stroke(ligne0[x]); //couleur du pixel line(x,310,x,350); //trace une ligne verticale }
stroke(255,0,0); //rouge
rectMode(CORNERS); //mode rectangle à 2 coordonnees (plutot que taille)

T. Grandpierre © / ESIEE | 58

rect (0,45,130,301); //rect rouge
}

void serialEvent (Serial maConnection) { // si des données arrivent par la connexion série
String myString = null;
int pixel; //valeur du pixel camera qu'on va lire sur le port serie
myString = maConnection.readStringUntil(32); //lecture sur port serie
if (myString !=null) {
myString = myString.substring(0, myString.length()-1); //pour retirer l'espace
if ( myString.equals("L:0")){ //chaine envoyée à chaque nouvelle image
//println("debut ligne"+i); //debub : affiche debut ligne et le compteur de pixels
i=0;
x=0;
} else {
i++;
x+=2;
try {
pixel = Integer.parseInt(myString); }
catch(NumberFormatException e){
pixel = 0;
}
pixel=pixel/16; //car ADC sur 12bits (MODE_12) donc 0 a 4096, on veux 0-255
ligne0[i]=pixel;
//print("pixel["+i+"]="+pixel+" "); //debuf affiche valeur

}
}
}

/************************FIN**************************************/

Il ne reste plus qu’à exécuter ce programme dans processing, puis de télécharger et exécuter le fo

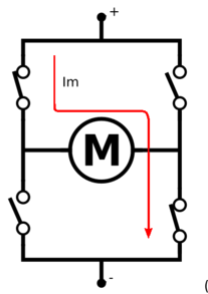
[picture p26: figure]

T. Grandpierre © / ESIEE | 59

## Annexe 2 – TPM Module : génération des PWMs moteur de propulsion

On fait varier la vitesse des moteurs à balais (par opposition aux sans balais/Brushless) en faisant varier leur tension d’alimentation. Pour faire varier une tension à l’aide d’un signal numérique, on utilise le plus souvent la modulation en largeur d’impulsion (MLI ou PWM Pulse Width Modulation).

(source Wikipedia)

Pour cela on génère un signal périodique (à quelques kilohertz généralement) dont le rapport de la durée de l’état haut par rapport à la durée de l’etat bas permet de faire varier la tension moyenne en sortie. Ce signal PWM pilote en général des transistors de puissance qui alimentent à leur tour les moteurs en « hachant » leur tension d’alimentation.

Afin de pouvoir inverser le sens de rotation des moteurs, il faut pouvoir inverser la polarité de l’alimentation aux bornes des moteurs. Pour cela on utilise des « ponts en H ». Ce nom vient de la forme en H qui apparait sur le schéma qui utilise alors au moins 4 transistors en mode commuté.

(source wikipedia)

T. Grandpierre © / ESIEE | 60

Au niveau logiciel il faut donc être capable de générer un signal PWM par moteur . Comme le pont en H comporte 2 parties à piloter en opposition de phase il faut finalement générer 2 signaux par moteur.

Pour cela il existe plusieurs techniques qui utilisent plus ou moins le processeur. Dans le cas des Kinetis il existe un périphérique dédié capable de générer ces signaux sans intervention du processeur (autre que sa configuration) : le TPM (Timer/PWM Module) décrit chapitre 31 du référence manual.

Dans le KL25Z il existe 3 instances de ce Timer, le TPM0, le TPM1 et le TPM2. Chaque PTM est capable de générer 4 signaux electriques externes indépendants mais utilisant la même base de temps. On parle de 4 canaux : C0, C1, C2 et C3.

Les 4 sorties PWM sont donc nommées : TPMx_C0SC, TPMx_C1SC, TPMx_C2SC, TPMx_C3SC.

Le code fournit par NxP utilise le TPM0 pour générer les signaux de PWM de propulsion. La fonction TFC_InitMotorPWM( ) initialise donc le TPM0 ainsi que les 4 canaux :

- TPM0_C0SC = TPM_CnSC_MSB_MASK | TPM_CnSC_ELSB_MASK;
- TPM0_C1SC = TPM_CnSC_MSB_MASK | TPM_CnSC_ELSA_MASK; // invert the second PWM
signal for a complimentary output;
- TPM0_C2SC = TPM_CnSC_MSB_MASK | TPM_CnSC_ELSB_MASK;
- TPM0_C3SC = TPM_CnSC_MSB_MASK | TPM_CnSC_ELSA_MASK; // invert the second PWM
signal for a complimentary output;

T. Grandpierre © / ESIEE | 61

Remarque : on a en effet besoin de piloter un pont en H par deux signaux en opposition de phase, les signaux TPM0_C1SC et TPM0_C3SC correspondent donc aux signaux TPM0_C0SC et TPM0_C2SC inversé)

Configuration des broches en sorties, connectées au PTM0 :

- PORTC_PCR1 = PORT_PCR_MUX(4);
- PORTC_PCR2 = PORT_PCR_MUX(4);
- PORTC_PCR3 = PORT_PCR_MUX(4);
- PORTC_PCR4 = PORT_PCR_MUX(4);

On note donc que ce sont les sorties PortC 1, 2, 3 et 4 qui sont dédiées à la commande moteur.

Le reste du code initialise différents registres ainsi que la fréquence PWM (ici 5 khz) :

void TFC_InitMotorPWM()
{
//Clock Setup for the TPM requires a couple steps.

//1st, set the clock mux
//See Page 124 of f the KL25 Sub-Family Reference Manual, Rev. 3, September 2012
SIM_SOPT2 |= SIM_SOPT2_PLLFLLSEL_MASK;// We Want MCGPLLCLK/2 (See Page 196 of the KL25 Sub-Family Reference Manual, Rev. 3, September 2012) SIM_SOPT2 &= ~(SIM_SOPT2_TPMSRC_MASK);
SIM_SOPT2 |= SIM_SOPT2_TPMSRC(1); //We want the MCGPLLCLK/2 (See Page 196 of the KL25 Sub-Family Reference Manual, Rev. 3, September 2012)

//Enable the Clock to the FTM0 Module
//See Page 207 of f the KL25 Sub-Family Reference Manual, Rev. 3, September 2012
SIM_SCGC6 |= SIM_SCGC6_TPM0_MASK;

//The TPM Module has Clock. Now set up the peripheral

//Blow away the control registers to ensure that the counter is not running
TPM0_SC = 0;
TPM0_CONF = 0;

//While the counter is disabled we can setup the prescaler

TPM0_SC = TPM_SC_PS(FTM0_CLK_PRESCALE);

//Setup the mod register to get the correct PWM Period

TPM0_MOD = FTM0_CLOCK/(1<<FTM0_CLK_PRESCALE)/FTM0_OVERFLOW_FREQUENCY;

//Setup Channels 0,1,2,3
TPM0_C0SC = TPM_CnSC_MSB_MASK | TPM_CnSC_ELSB_MASK;

T. Grandpierre © / ESIEE | 62
TPM0_C1SC = TPM_CnSC_MSB_MASK | TPM_CnSC_ELSA_MASK; // invert the
second PWM signal for a complimentary output;
TPM0_C2SC = TPM_CnSC_MSB_MASK | TPM_CnSC_ELSB_MASK;
TPM0_C3SC = TPM_CnSC_MSB_MASK | TPM_CnSC_ELSA_MASK; // invert the
second PWM signal for a complimentary output;

//Enable the Counter

//Set the Default duty cycle to 50% duty cycle TFC_SetMotorPWM(0.0,0.0);

//Enable the TPM COunter
TPM0_SC |= TPM_SC_CMOD(1);

//Enable the FTM functions on the the port PORTC_PCR1 = PORT_PCR_MUX(4);
PORTC_PCR2 = PORT_PCR_MUX(4);
PORTC_PCR3 = PORT_PCR_MUX(4);
PORTC_PCR4 = PORT_PCR_MUX(4);

}

Une fois la configuration terminée, le changement de vitesse de rotation des moteurs s’effectue en modifiant la valeur des registres du PTM0 correspondant (en rouge ci-dessous) :

void TFC_SetMotorPWM(float MotorA , float MotorB)
{
if(MotorA>1.0)
MotorA = 1.0;
else if(MotorA<-1.0)
MotorA = -1.0;

if(MotorB>1.0)
MotorB = 1.0;
else if(MotorB<-1.0)
MotorB = -1.0;

TPM0_C2V = (uint16_t) ((float)TPM0_MOD * (float)((MotorA + 1.0)/2.0));
TPM0_C3V = TPM0_C2V;
TPM0_C0V = (uint16_t) ((float)TPM0_MOD * (float)((MotorB + 1.0)/2.0));
TPM0_C1V = TPM0_C0V;

}

T. Grandpierre © / ESIEE | 63

## Annexe 3 – TPM Module : génération des PWMs pour servomoteur

Le servomoteur utilisé dans les chassis Alamak et Model C sont des servomoteurs de modélisme dont la position angulaire est commandée à l’aide d’une PWM. Il est possible de controler la rotation de l’arbre de sortie de ces servos sur une plage de -90° à +90°, la position neutre étant 0°.

On pilote ces servo au moyen de 3 fils : 2 pour l’alimentation (qui peut aller de 5 à 7,2v), et un fil de commande.

Pour placer l’arbre de sortie de ces servos au neutre (0°) il faut envoyer un créneau de 1,5 millisecondes à la période de 20ms.

Pour le faire tourner à droite il faut allonger la durée de ce créneau, le maximum étant un créneau de 2ms pour une rotation maximum de +90°.

Inversement, pour le faire tourner dans l’autre sens il suffit de diminuer la durée du créneau, jusqu’à un minimum de 1ms.

(source Wikipédia)

Comme pour les moteurs de propulsion, nous allons utiliser le périphérique PTM pour piloter les servos. La différence sera principalement dans la fréquence du signal qui sera cette fois beaucoup plus faible puisque 20ms contre 5 khz.

Le principe de configuration reste donc le même, le code utilise cette fois le TPM1 configuré à 50 hz (20 ms). Le code ci-dessous indique que ce sont les sorties 0 et 1 du port B qui seront utilisées pour piloter les servos.

void TFC_InitServos()
{

//Clock Setup for the TPM requires a couple steps.

T. Grandpierre © / ESIEE | 64
//1st, | set the clock mux
//See Page 124 of f the KL25 Sub-Family Reference Manual, Rev. 3, September 2012
SIM_SOPT2 |= SIM_SOPT2_PLLFLLSEL_MASK;// We Want MCGPLLCLK/2 (See Page 196 of the KL25 Sub-Family Reference Manual, Rev. 3, September 2012) SIM_SOPT2 &= ~(SIM_SOPT2_TPMSRC_MASK);
SIM_SOPT2 |= SIM_SOPT2_TPMSRC(1); //We want the MCGPLLCLK/2 (See Page 196 of the KL25 Sub-Family Reference Manual, Rev. 3, September 2012)

//Enable the Clock to the FTM0 Module
//See Page 207 of f the KL25 Sub-Family Reference Manual, Rev. 3, September 2012
SIM_SCGC6 |= SIM_SCGC6_TPM1_MASK;

//The TPM Module has Clock. Now set up the peripheral

//Blow away the control registers to ensure that the counter is not running TPM1_SC = 0;
TPM1_CONF = 0;

//While the counter is disabled we can setup the prescaler

TPM1_SC = TPM_SC_PS(FTM1_CLK_PRESCALE);
TPM1_SC |= TPM_SC_TOIE_MASK; //Enable Interrupts for the Timer Overflow

//Setup the mod register to get the correct PWM Period

TPM1_MOD = FTM1_CLOCK/(1<<(FTM1_CLK_PRESCALE+1))/FTM1_OVERFLOW_FREQUENCY;

//Setup Channels 0 and 1

TPM1_C0SC = TPM_CnSC_MSB_MASK | TPM_CnSC_ELSB_MASK;
TPM1_C1SC = TPM_CnSC_MSB_MASK | TPM_CnSC_ELSB_MASK;

//Enable the Counter

//Set the Default duty cycle to servo neutral TFC_SetServo(0, 0.0);
TFC_SetServo(1, 0.0);

//Enable the TPM COunter
TPM1_SC |= TPM_SC_CMOD(1);

//Enable TPM1 IRQ on the NVIC
enable_irq (INT_TPM1-16);

//Enable the FTM functions on the the port

PORTB_PCR0 = PORT_PCR_MUX(3);
PORTB_PCR1 = PORT_PCR_MUX(3);
}

T. Grandpierre © / ESIEE | 65

La fonction TFC_SetServo permet ensuite de piloter la position des servos.

//Position is -1.0 to 1.0. | Use SERVO_X_MIN_DUTY_CYCLE and
SERVO_MAX_DUTY_CYCLE | to calibrate the extremes
void TFC_SetServo(uint8_t ServoNumber, float Position)
{
TFC_SetServoDutyCycle(ServoNumber , (((Position +
1.0)/2)*(SERVO_MAX_DUTY_CYCLE -SERVO_MIN_DUTY_CYCLE))+SERVO_MIN_DUTY_CYCLE);

}

T. Grandpierre © / ESIEE | 66

## Annexe 4 – Récapitulatif de l’affectation des broches

Camera 0 et 1 (3.3v sur br 4, gnd vr. 5)

- IA br 1 camera 0 : chanel 6 ADC0 –PTD5 ADC0_SE6b
- IA br 1 camera 1: PTD 6 ADC0_SE7b
- SI br 2 : PTD7 (commun aux 2 cameras)
- Clk br 3 : PTE1(commun aux 2 cameras)

Speed sensor :

- PTA1/FTM2 CH0 br 2 (pullup 3.3)
- PTA2/FTM2 CH1 br 2 (pullup 3.3)

Servos :

- PTB0_FTM1_CH0
- PTB1_FTM0_CH1

Potentiomètres :

- POT0 : PTB3 ADC0_SE13 (100k 3,3v)
- POT1 : PTB2 ADC0_SE12 idem

Batterie :

- pont div. 47k/10k sur PTE29 ADC0_SE4b

Switchs :

- sw1 PTC13, pulldown
- sw2 PTC17 pulldown
- 4 dip-switchs : (pulldown ouvert)
- 1 sur PTE2, PTE3, PTE4, PTE5
- 4 leds : PTB8, PTB9, PTB10, PTB11

Bridge PWM :

- PTC3-FTM0 CH2 = IN1 moteur1
- PTC3-FTM0 CH3 = IN2 moteur 1
- PTE23 ADC0_SE7a = retour courant M1
- PE21 : H bridge enable (commun aux 2)
- PTE20 : Fault
- PTC1 FTM0_CH0 = IN1 moteur 2
- PTC2 FTM0_CH1 = IN2 moteur2
- PTE22 ADC0_SE3 = retour courant M2

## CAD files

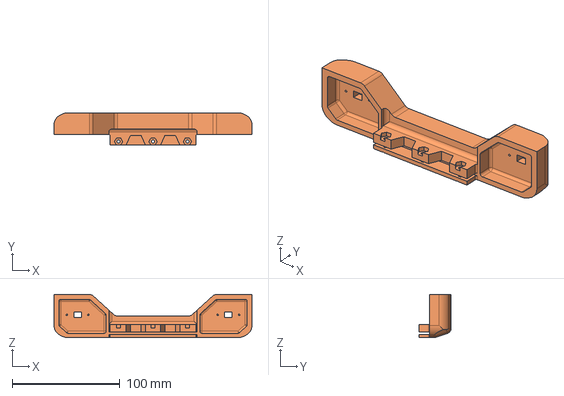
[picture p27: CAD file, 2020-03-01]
meca/Inventor/PareChoc.stp
184.0 x 30.0 x 40.0 mm

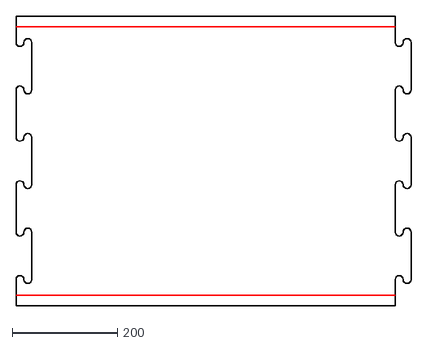
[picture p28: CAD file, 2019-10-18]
meca/Piste/Droit.dxf
750.0 x 550.0

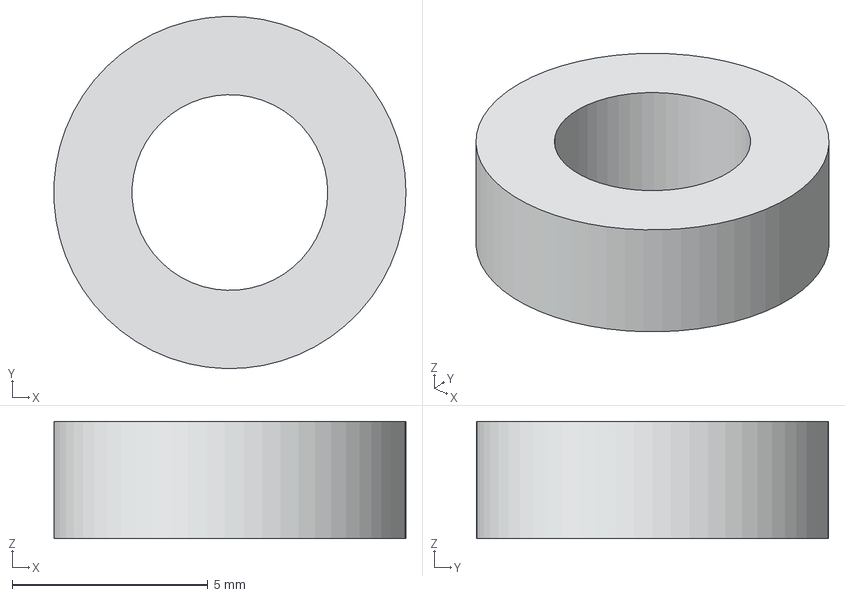
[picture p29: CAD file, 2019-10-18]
meca/Roulement.FCStd
8.99 x 9.00 x 3.00 mm

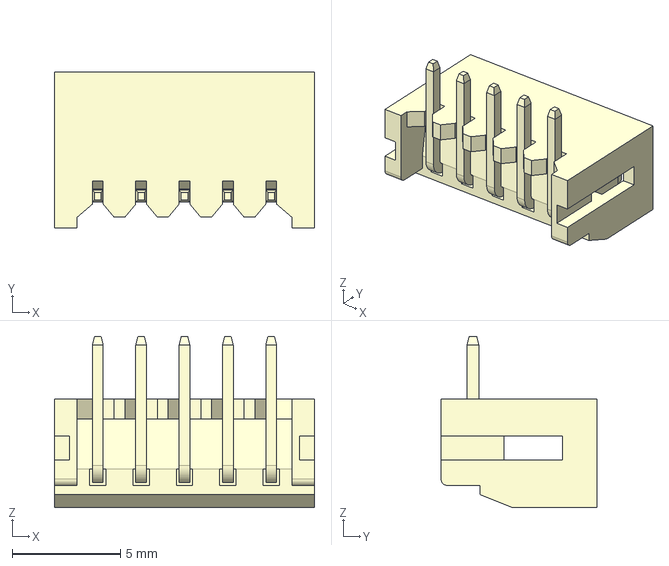
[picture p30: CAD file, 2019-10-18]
pcb/Modeles 3D/DF3-5P-2DS.stp
12.0 x 7.20 x 7.90 mm

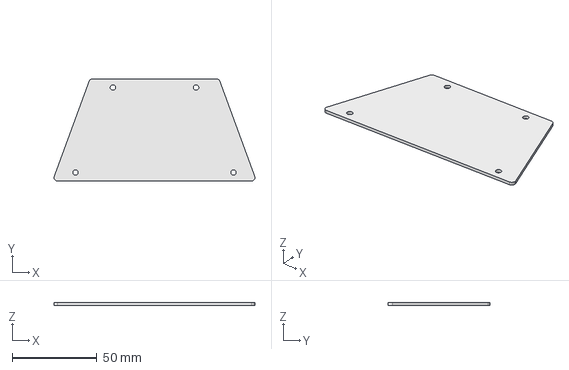
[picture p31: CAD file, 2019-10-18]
meca/Carte_puissance.fcstd
118.3 x 60.0 x 1.60 mm

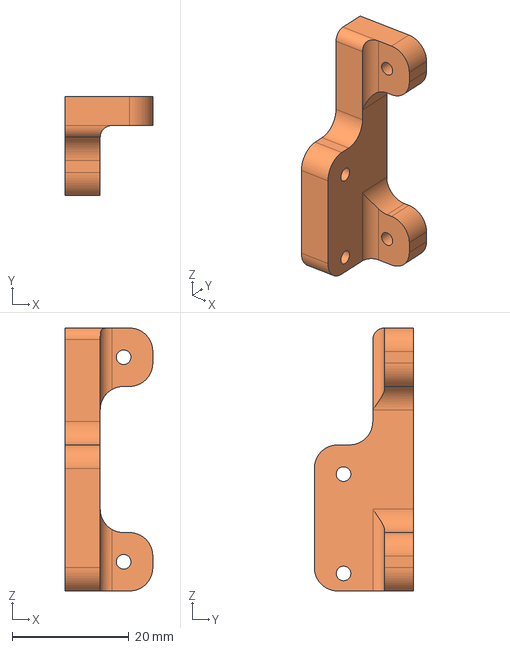
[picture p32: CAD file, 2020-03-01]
meca/Inventor/EquerrePCBDroite.stp
15.0 x 17.0 x 45.0 mm

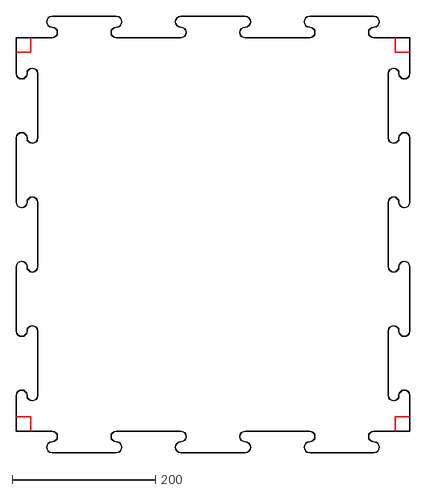
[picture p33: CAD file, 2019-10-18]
meca/Piste/Intersection.dxf
550.0 x 610.0

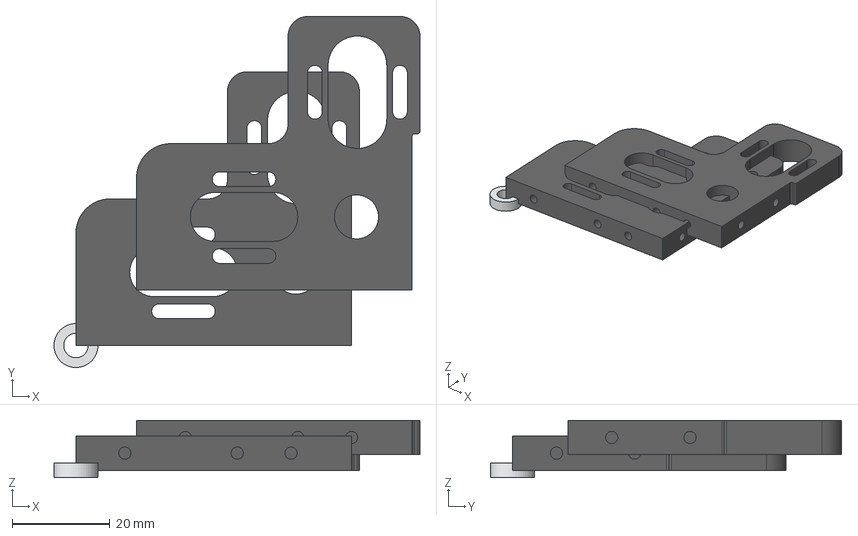
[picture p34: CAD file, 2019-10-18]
meca/Alamak.FCStd
74.9 x 71.8 x 11.7 mm
Roulement
Roulement2
Support Moteur
Support Moteur001

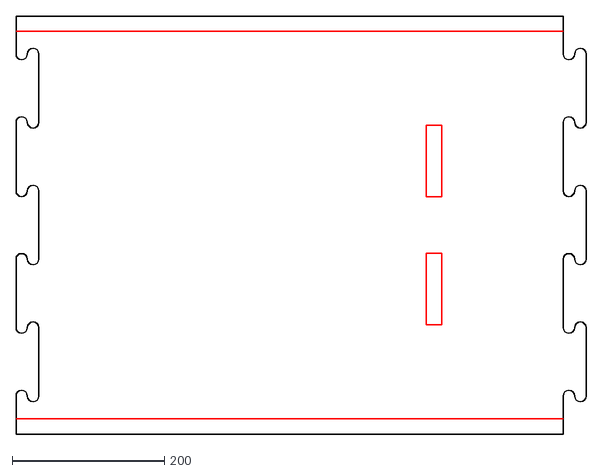
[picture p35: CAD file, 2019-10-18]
meca/Piste/Droit-Arrivee.dxf
750.0 x 550.0

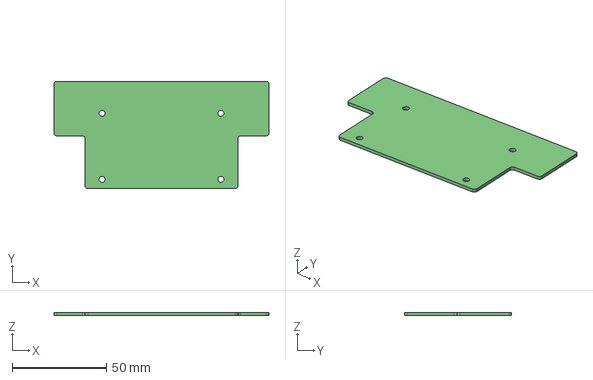
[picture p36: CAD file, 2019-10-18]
meca/Inventor/PCBPuissance.stp
114.0 x 57.0 x 1.60 mm

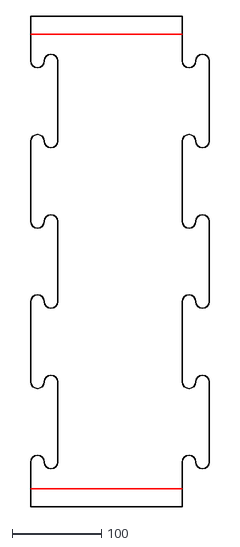
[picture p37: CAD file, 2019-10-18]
meca/Piste/Droit-Court.dxf
200.0 x 550.0

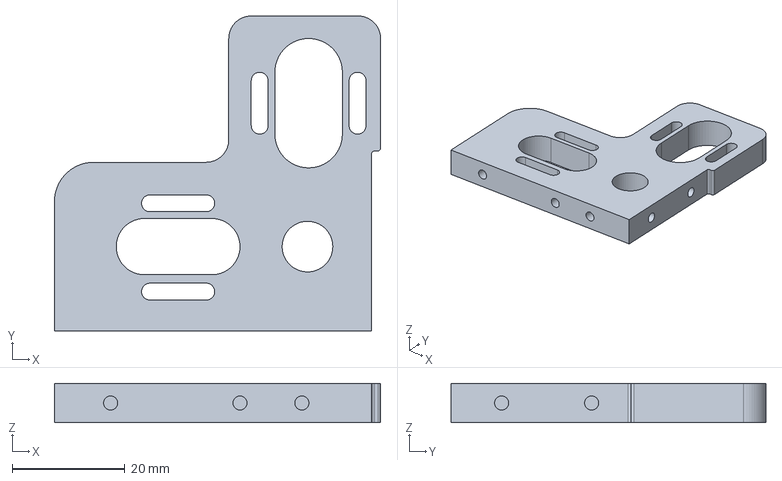
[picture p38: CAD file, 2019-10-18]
meca/Support_Moteur.FCStd
58.0 x 56.0 x 7.00 mm

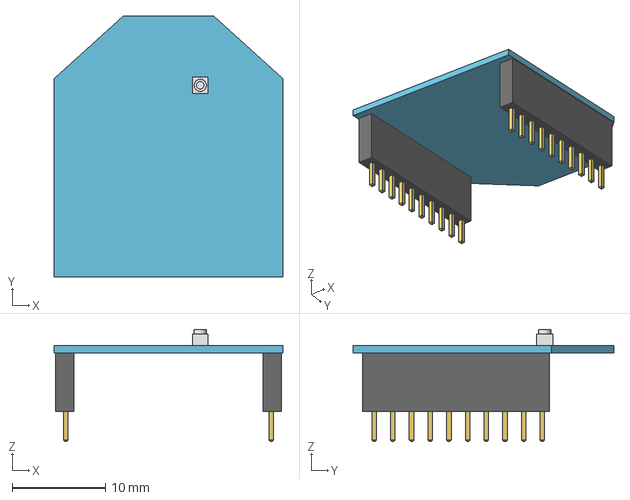
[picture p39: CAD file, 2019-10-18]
meca/Inventor/Xbee.stp
24.5 x 27.9 x 12.0 mm

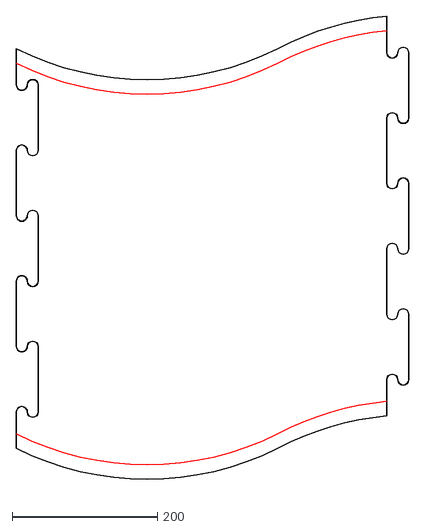
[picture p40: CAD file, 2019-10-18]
meca/Piste/Chicane.dxf
540.0 x 651.6

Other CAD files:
meca/Inventor/EquerrePCBGauche.stp
pcb/Modeles 3D/c-2213738-4-1-3d.stp
meca/Inventor/PCBCapteurs.stp
meca/Piste/Virage.dxf
meca/Carte_Puissance.dxf
meca/Inventor/Alamak.iam
meca/Inventor/AxeArriere.ipt
meca/Inventor/Base.ipt
meca/Inventor/Batterie.ipt
meca/Inventor/Content Center/E4T-X-236-S-H-M-X.ipt
meca/Inventor/Content Center/fr-FR/ANSI B 18.2.4.1 M(1)/ANSI B 18.2.4.1 M - M2,5 x 0,45Style 1.ipt
meca/Inventor/Content Center/fr-FR/ANSI B 18.2.4.1 M(1)/ANSI B 18.2.4.1 M - M3 x 0,5Style 1.ipt
meca/Inventor/Content Center/fr-FR/ANSI B 18.2.4.1 M(1)/ANSI B 18.2.4.1 M - M3 x 0,5Style 2.ipt
meca/Inventor/Content Center/fr-FR/ANSI B18.16.3M(2)/ANSI B18.16.3M - Property Class 5 and 10 - Metric M3.5 x 0.6 Type de métal.ipt
meca/Inventor/Content Center/fr-FR/ISO 7046-2 H/ISO 7046-2 H - M2.5x3 - 8.8 - H1.ipt
meca/Inventor/Content Center/fr-FR/ISO 7046-2 H/ISO 7046-2 H - M2.5x5 - 8.8 - H1.ipt
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

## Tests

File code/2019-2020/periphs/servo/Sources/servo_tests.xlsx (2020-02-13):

 | T | 14.7 | cm
 | L | 18.5 | cm
 | R | 29 | cm
 | alpha1 | 0.707102754 | rad | 40.51400348 | °
 | alpha2 | 0.4707746813 | rad | 26.97340234 | ° | 33.74370291 | °
 | alpha1 | 26
 | alpha2 | 19
 | R | 45.28062107 | cm | R2 | 46.37790124 | cm
 | theta | rmeas | Rreal | theta real 1
theta max neg | 22 | 62.3 | 38.5 | 30.71 | 21.97 | 25.67 |  |  |  | 1.113636364
consigne | -20 | 82.4 | 48.55 | 24.18 | 18.31 | 20.86 |  |  |  | 750
 | -15 | 124.8 | 71.65 | 16.05 | 13.18 | 14.48 |  |  |  | 835.2272727
 | -10 | 214.4 | 107.2 | 10.50 | 9.17 | 9.79 |  |  |  | 8085.227273
 | 0 | inf
 | 10 | 206.2 | 103.1 | 10.94 | 9.51 | 10.17
 | 15 | 133.4 | 67.05355138 | 17.22 | 13.96 | 15.42
 | 20 | 93.2 | 46.83538734 | 25.10 | 18.85 | 21.55
 | 25 | 68 | 34 | 34.77 | 24.10 | 28.55 |  | 0.8756140545
theta max pos | 29 | 51.3 | 33 | 35.80 | 24.63 | 29.28
 | theta | rmeas | Rreal | theta real 1
 |  |  |  |  |  |  |  | 6500 | 6593
consigne | -24.5 | 60.5 | 37.6 | 31.45 | 22.37 | 26.20 |  | 28.55
 | -15 |  | 7.35 | #DIV/0! | 51.53 | 68.33
 | -10 |  | 7.35 | #DIV/0! | 51.53 | 68.33
 | 0 |  | 7.35
 | 10 |  | 7.35 | #DIV/0! | 51.53 | 68.33
 | 15 | 115 | 64.85 | 17.84 | 14.37 | 15.92
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

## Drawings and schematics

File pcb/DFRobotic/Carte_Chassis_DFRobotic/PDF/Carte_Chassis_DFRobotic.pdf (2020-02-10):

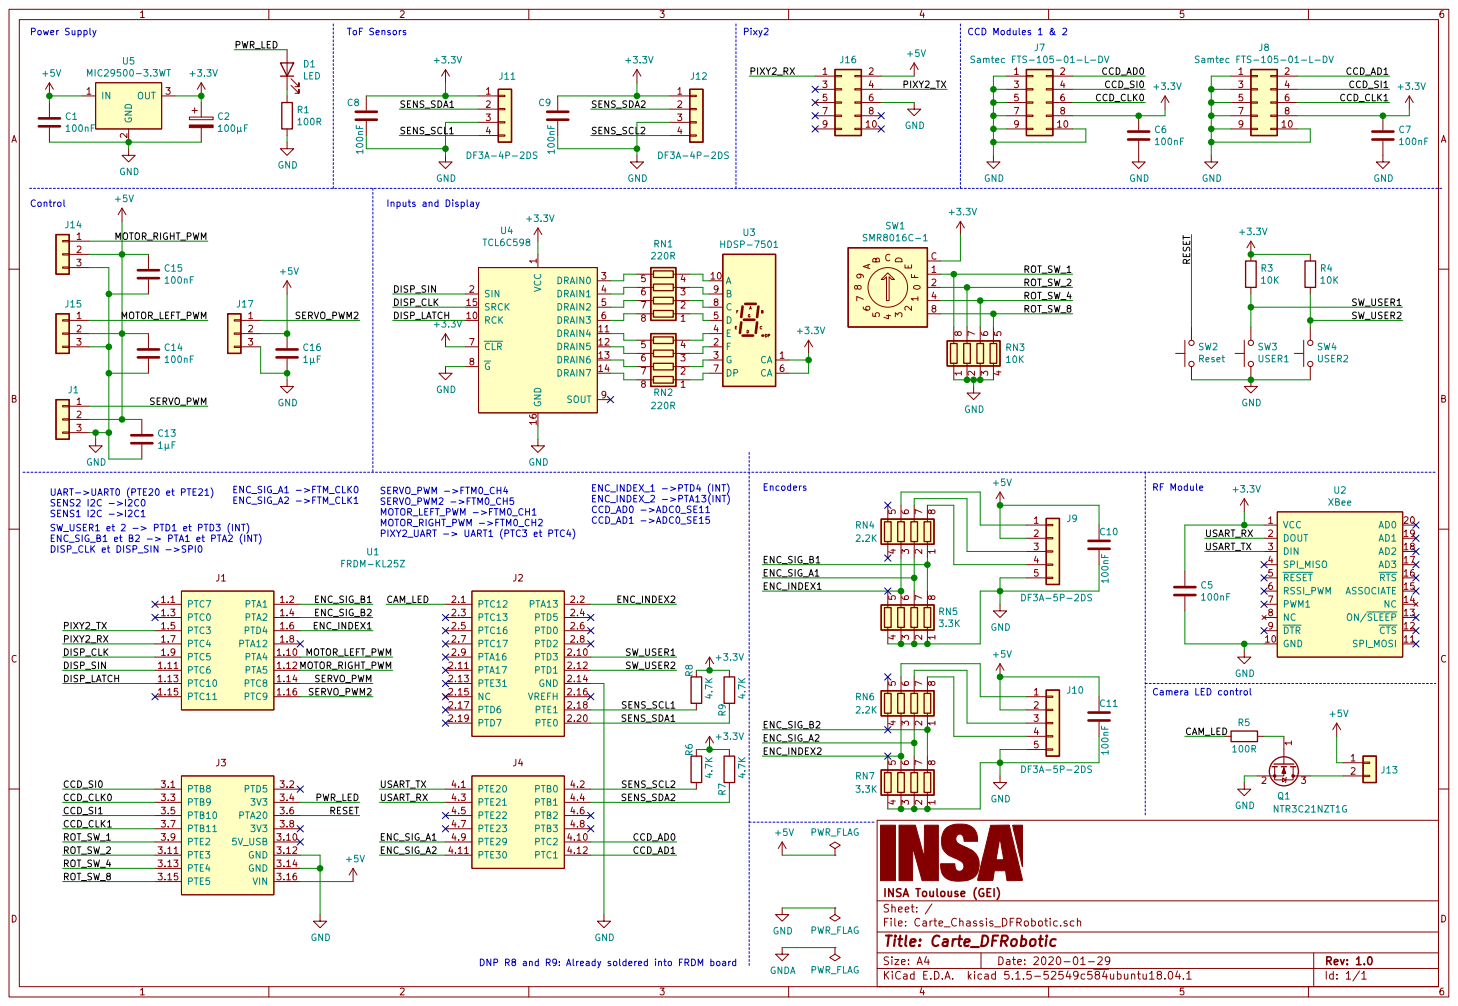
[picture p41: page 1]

1 RCK 10 DRAIN4 11 DRAIN5 12 DRAIN6 13 DRAIN7 14 SRCK 15 GND 16 SIN 2 DRAIN0 3 DRAIN1 4 DRAIN2 5 DRAIN3 6 CLR 7 G

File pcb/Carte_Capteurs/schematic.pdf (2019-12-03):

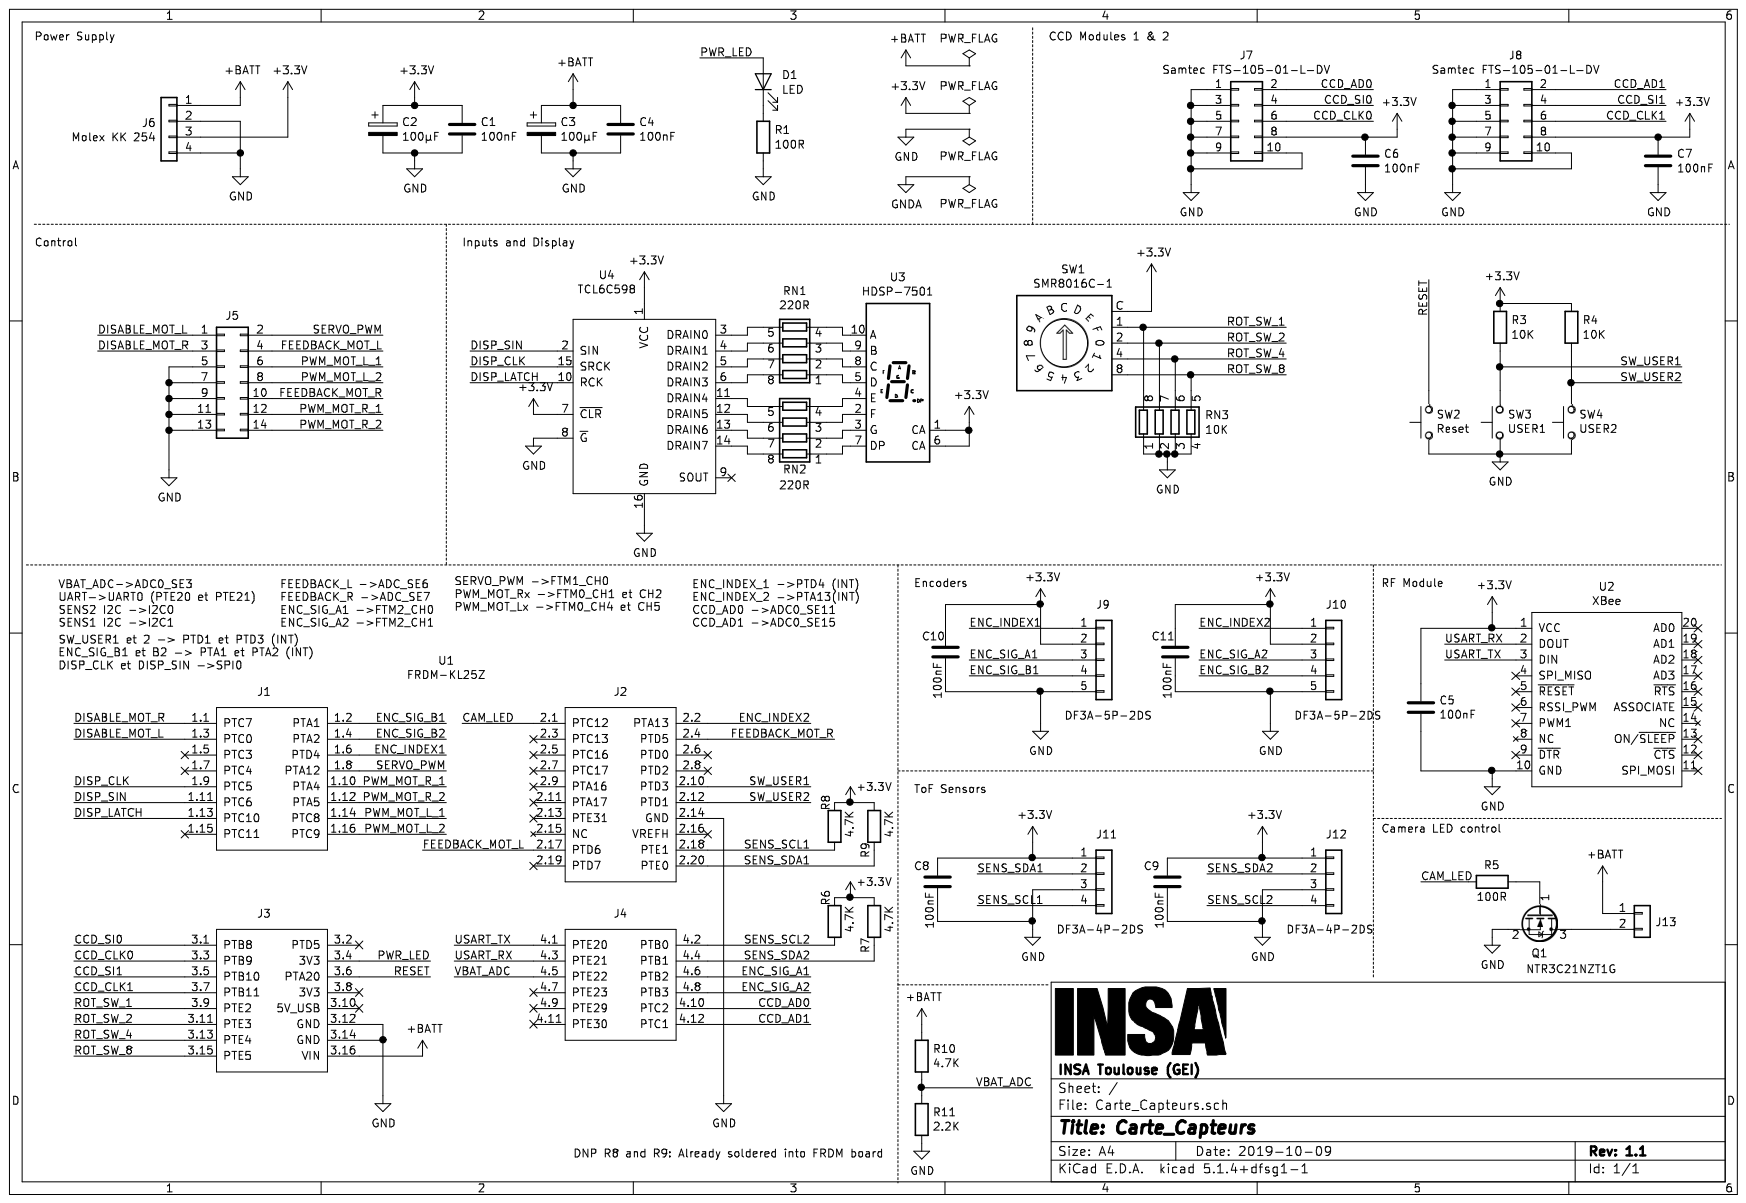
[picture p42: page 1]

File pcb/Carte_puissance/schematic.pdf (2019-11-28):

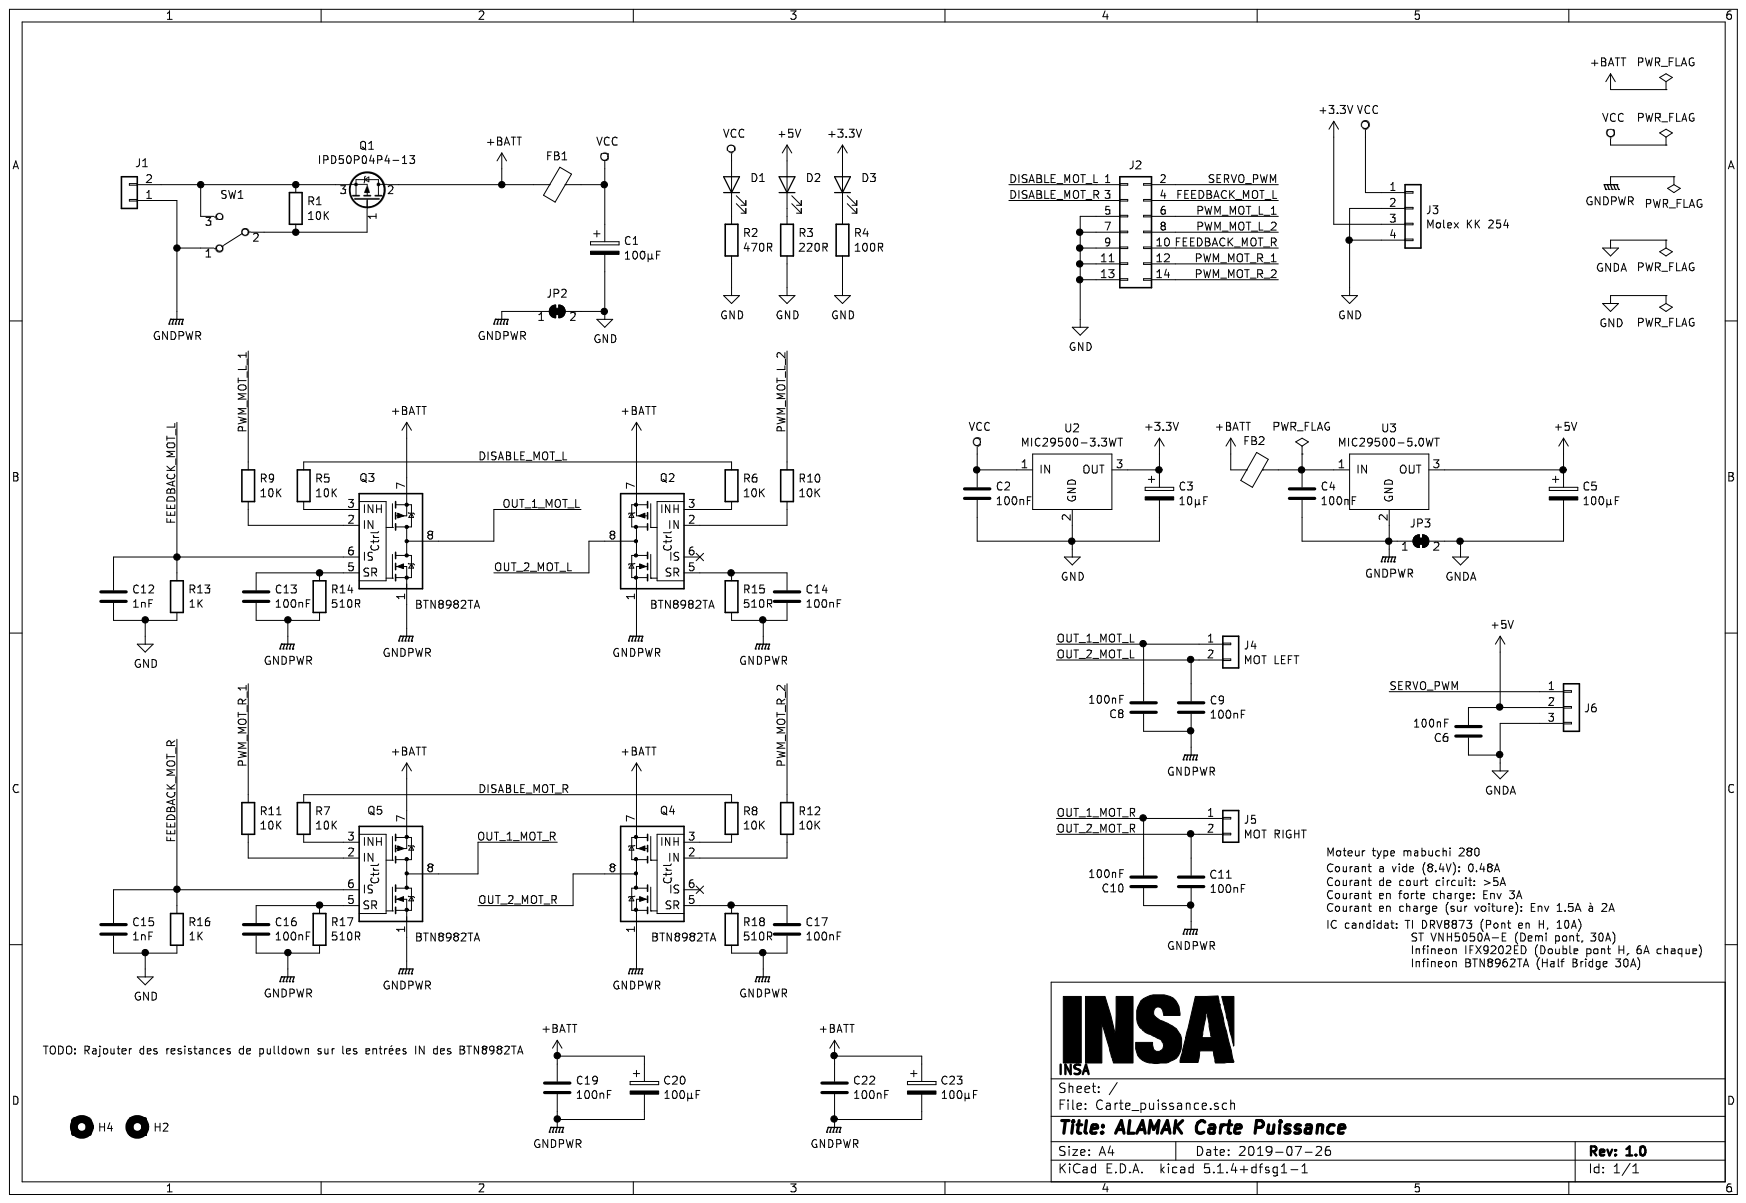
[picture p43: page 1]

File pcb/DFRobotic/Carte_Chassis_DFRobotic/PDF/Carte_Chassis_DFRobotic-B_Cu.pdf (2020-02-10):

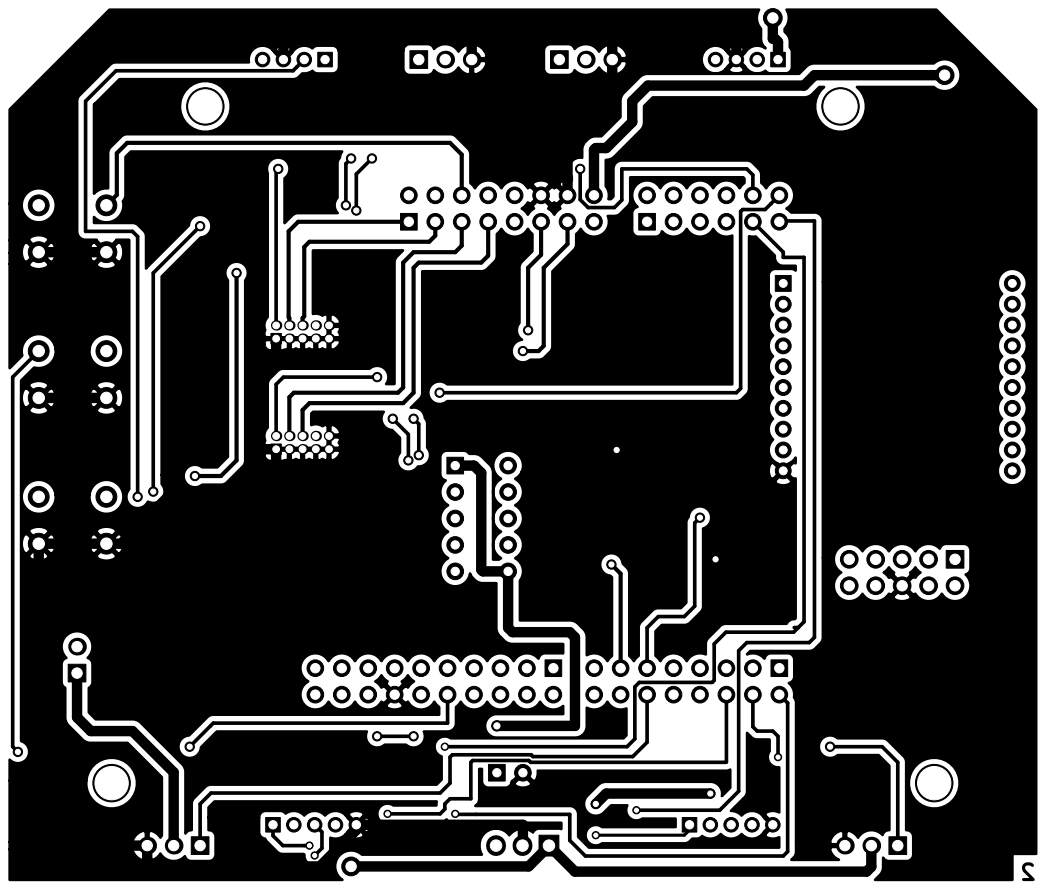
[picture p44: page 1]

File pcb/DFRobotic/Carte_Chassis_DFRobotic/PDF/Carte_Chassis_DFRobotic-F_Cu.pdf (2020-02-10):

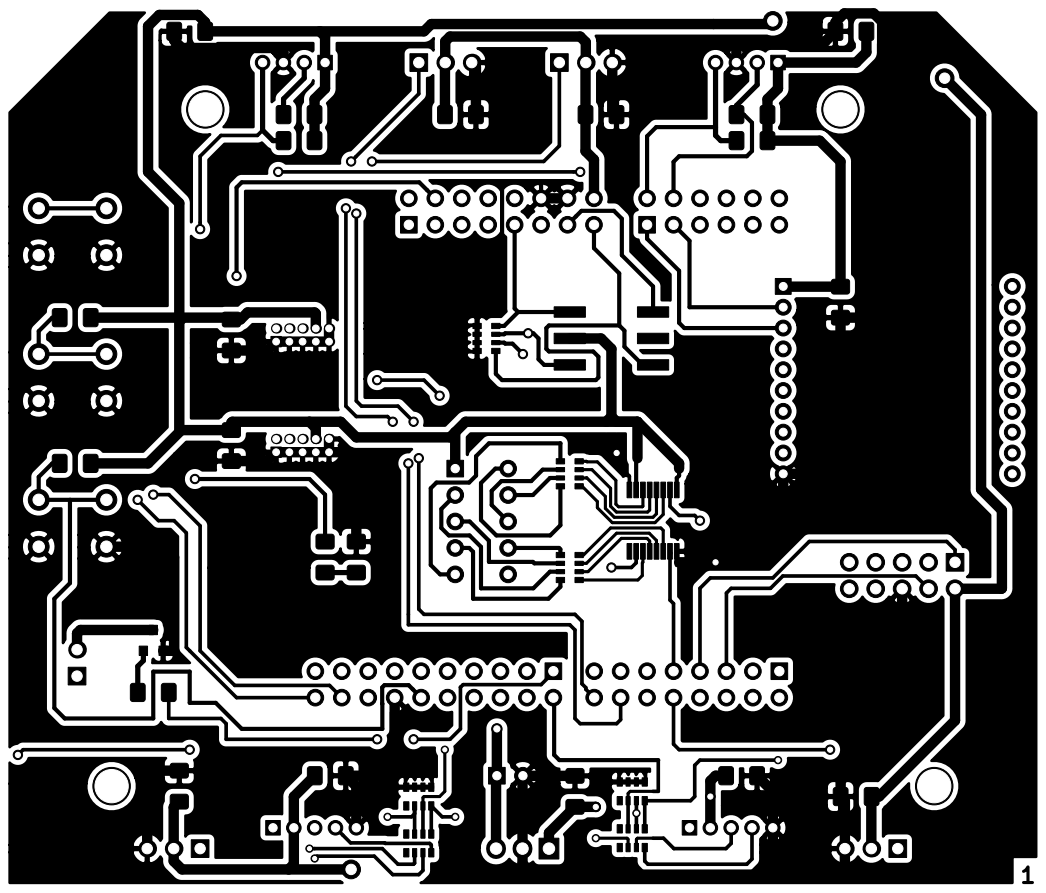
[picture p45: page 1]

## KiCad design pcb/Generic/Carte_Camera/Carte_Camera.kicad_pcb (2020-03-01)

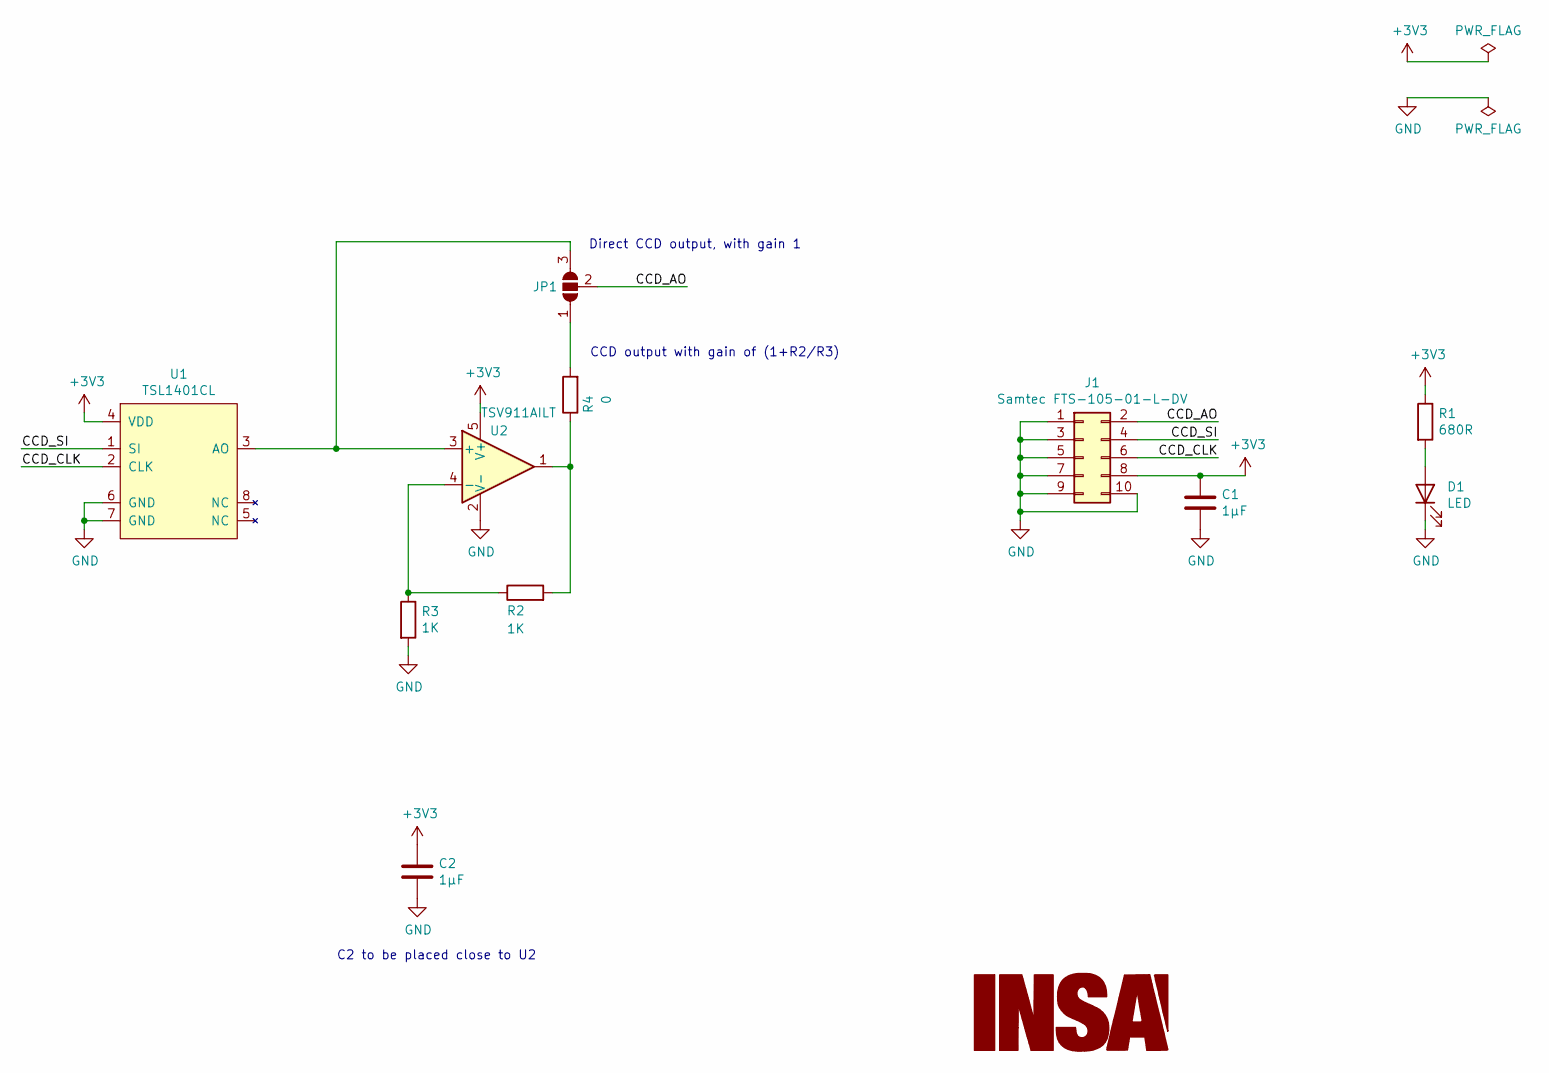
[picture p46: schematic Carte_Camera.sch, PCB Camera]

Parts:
C1, C2: 1µF; C_0805_2012Metric_Pad1.15x1.40mm_HandSolder
D1: LED; LED_0805_2012Metric_Pad1.15x1.40mm_HandSolder
J1: Samtec FTS-105-01-L-DV; PinHeader_2x05_P1.27mm_Vertical
JP1: SolderJumper_3_Open; SolderJumper-3_P1.3mm_Open_RoundedPad1.0x1.5mm_NumberLabels
R1: 680R; R_0805_2012Metric_Pad1.15x1.40mm_HandSolder
R2, R3: 1K; R_0805_2012Metric_Pad1.15x1.40mm_HandSolder
R4: 0; R_0805_2012Metric_Pad1.15x1.40mm_HandSolder
U1: TSL1401CL
U2: TSV911AILT; SOT-23-5

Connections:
+3V3: C1.1, C2.1, J1.8, R1.1, U1.4 (VDD), U2.5 (V+)
/CCD_AO: J1.2, JP1.2 (C)
/CCD_CLK: J1.6, U1.2 (CLK)
/CCD_SI: J1.4, U1.1 (SI)
GND: C1.2, C2.2, D1.1 (K), J1.1, J1.3, J1.5, J1.7, J1.9, J1.10, R3.2, U1.6 (GND), U1.7 (GND), U2.2 (V-)
unnamed: D1.2 (A), R1.2
unnamed: JP1.1 (A), R4.2
unnamed: JP1.3 (B), U1.3 (AO), U2.3 (+)
unnamed: R2.1, R3.1, U2.4 (-)
unnamed: R2.2, R4.1, U2.1

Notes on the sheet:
Direct CCD output, with gain 1
CCD output with gain of (1+R2/R3)
C2 to be placed close to U2

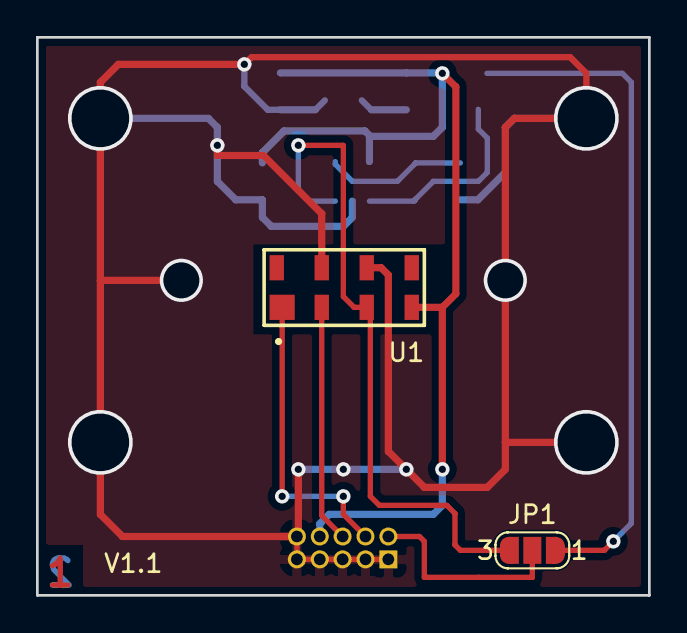
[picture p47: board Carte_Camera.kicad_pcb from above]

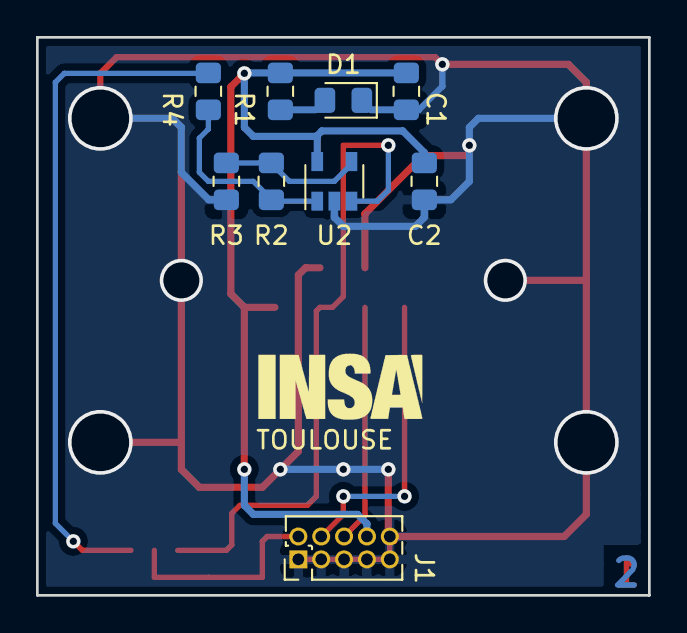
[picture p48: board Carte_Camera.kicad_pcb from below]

Board: 2 copper layers, 34.0 x 31.0 mm, 12 parts (10 on the bottom side), 10 nets.

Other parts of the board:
G1: LOGO; insa-image

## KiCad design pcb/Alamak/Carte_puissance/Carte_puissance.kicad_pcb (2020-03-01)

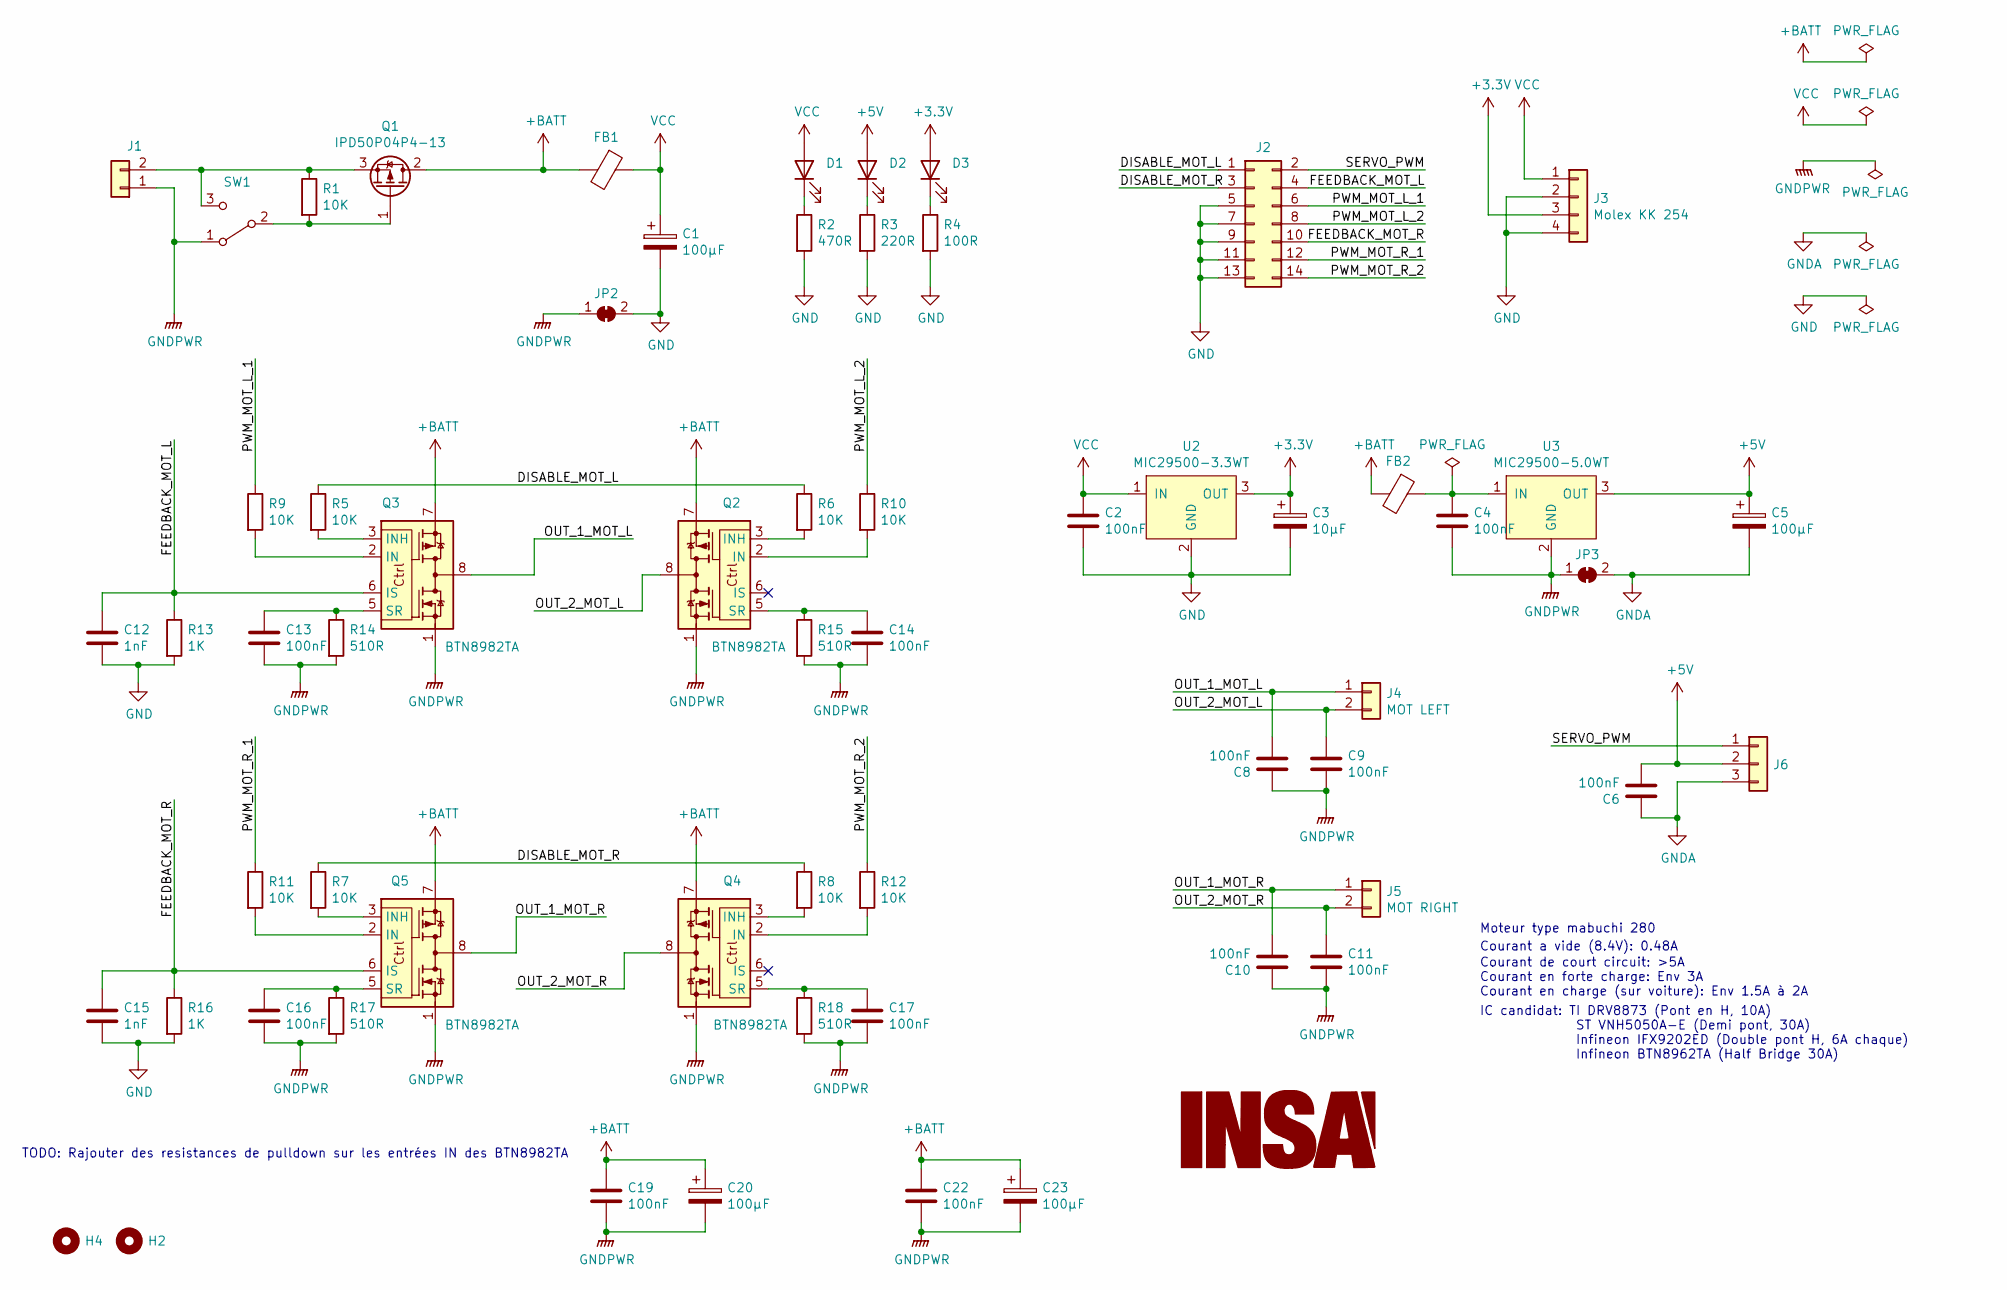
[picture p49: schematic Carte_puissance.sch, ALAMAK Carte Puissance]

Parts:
C1, C5, C20, C23: 100µF; CP_Radial_D6.3mm_P2.50mm
C2, C4, C6, C8, C9, C10, C11, C13, C14, C16, C17, C19, C22: 100nF; C_1206_3216Metric_Pad1.42x1.75mm_HandSolder
C3: 10µF; CP_Radial_D5.0mm_P2.00mm
C12, C15: 1nF; C_1206_3216Metric_Pad1.42x1.75mm_HandSolder
D1, D2, D3: LED; LED_D3.0mm
FB1, FB2: Ferrite_Bead; C_1812_4532Metric_Pad1.30x3.40mm_HandSolder
H2, H4: MountingHole; MountingHole_3.2mm_M3
J1: Conn_01x02; SolderWirePad_1x02_P7.62mm_Drill2mm
J2: Conn_02x07_Odd_Even; Multicomp_MC9A12-1434_2x07_P2.54mm_Vertical
J3: Molex KK 254; Molex_KK-254_AE-6410-04A_1x04_P2.54mm_Vertical
J4: MOT LEFT; JST_VH_B2PS-VH_1x02_P3.96mm_Horizontal
J5: MOT RIGHT; JST_VH_B2PS-VH_1x02_P3.96mm_Horizontal
J6: Conn_01x03; SolderWirePad_1x03_P3.175mm_Drill1mm
JP2, JP3: SolderJumper_2_Bridged; SolderJumper-2_P1.3mm_Bridged2Bar_RoundedPad1.0x1.5mm
Q1: IPD50P04P4-13; TO-252-2
Q2, Q3, Q4, Q5: BTN8982TA; TO-263-7_TabPin8
R1, R5, R6, R7, R8, R9, R10, R11, R12: 10K; R_1206_3216Metric_Pad1.42x1.75mm_HandSolder
R2: 470R; R_1206_3216Metric_Pad1.42x1.75mm_HandSolder
R3: 220R; R_1206_3216Metric_Pad1.42x1.75mm_HandSolder
R4: 100R; R_1206_3216Metric_Pad1.42x1.75mm_HandSolder
R13, R16: 1K; R_1206_3216Metric_Pad1.42x1.75mm_HandSolder
R14, R15, R17, R18: 510R; R_1206_3216Metric_Pad1.42x1.75mm_HandSolder
SW1: SW_SPDT; SW_Slide_1P2T_CK_OS102011MS2Q
U2: MIC29500-3.3WT; TO-220-3_Horizontal_TabDown
U3: MIC29500-5.0WT; TO-220-3_Horizontal_TabDown

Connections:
+3V3: C3.1, D3.2 (A), J3.3, U2.3 (OUT)
+5V: C5.1, C6.2, D2.2 (A), J6.2, U3.3 (OUT)
+BATT: C19.1, C20.1, C22.1, C23.1, FB1.2, FB2.2, Q1.2 (D), Q2.7, Q3.7, Q4.7, Q5.7
/DISABLE_MOT_L: J2.1, R5.1, R6.1
/DISABLE_MOT_R: J2.3, R7.1, R8.1
/FEEDBACK_MOT_L: C12.1, J2.4, Q3.6 (IS), R13.1
/FEEDBACK_MOT_R: C15.1, J2.10, Q5.6 (IS), R16.1
/OUT_1_MOT_L: C8.2, J4.1, Q3.4, Q3.8
/OUT_1_MOT_R: C10.2, J5.1, Q5.4, Q5.8
/OUT_2_MOT_L: C9.1, J4.2, Q2.4, Q2.8
/OUT_2_MOT_R: C11.1, J5.2, Q4.4, Q4.8
/PWM_MOT_L_1: J2.6, R9.1
/PWM_MOT_L_2: J2.8, R10.1
/PWM_MOT_R_1: J2.12, R11.1
/PWM_MOT_R_2: J2.14, R12.1
/SERVO_PWM: J2.2, J6.1
GND: C1.2, C2.2, C3.2, C12.2, C15.2, J2.5, J2.7, J2.9, J2.11, J2.13, J3.2, J3.4, JP2.2 (B), R2.2, R3.2, R4.2, R13.2, R16.2, U2.2 (GND)
GNDA: C5.2, C6.1, J6.3, JP3.2 (B)
GNDPWR: C4.2, C8.1, C9.2, C10.1, C11.2, C13.2, C14.2, C16.2, C17.2, C19.2, C20.2, C22.2, C23.2, J1.1, JP2.1 (A), JP3.1 (A), Q2.1, Q3.1, Q4.1, Q5.1, R14.2, R15.2, R17.2, R18.2, SW1.1 (A), U3.2 (GND)
unnamed: C4.1, FB2.1, U3.1 (IN)
unnamed: C13.1, Q3.5 (SR), R14.1
unnamed: C14.1, Q2.5 (SR), R15.1
unnamed: C16.1, Q5.5 (SR), R17.1
unnamed: C17.1, Q4.5 (SR), R18.1
unnamed: D1.1 (K), R2.1
unnamed: D2.1 (K), R3.1
unnamed: D3.1 (K), R4.1
unnamed: J1.2, Q1.3 (S), R1.1, SW1.3 (C)
unnamed: Q1.1 (G), R1.2, SW1.2 (B)
unnamed: Q2.2 (IN), R10.2
unnamed: Q2.3 (INH), R6.2
unnamed: Q3.2 (IN), R9.2
unnamed: Q3.3 (INH), R5.2
unnamed: Q4.2 (IN), R12.2
unnamed: Q4.3 (INH), R8.2
unnamed: Q5.2 (IN), R11.2
unnamed: Q5.3 (INH), R7.2
VCC: C1.1, C2.1, D1.2 (A), FB1.1, J3.1, U2.1 (IN)

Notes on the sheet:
Moteur type mabuchi 280
Courant a vide (8.4V): 0.48A
Courant de court circuit: >5A Courant en forte charge: Env 3A Courant en charge (sur voiture): Env 1.5A à 2A
IC candidat: TI DRV8873 (Pont en H, 10A) ST VNH5050A-E (Demi pont, 30A) Infineon IFX9202ED (Double pont H, 6A chaque) Infineon BTN8962TA (Half Bridge 30A)
TODO: Rajouter des resistances de pulldown sur les entrées IN des BTN8982TA

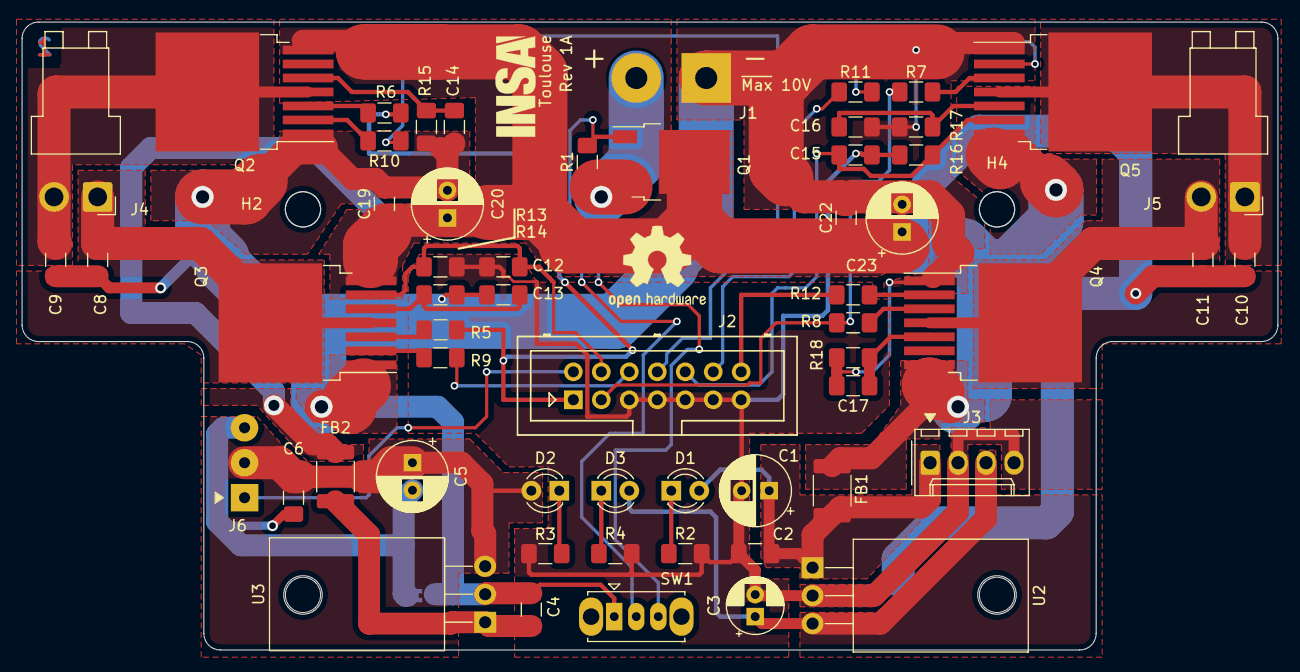
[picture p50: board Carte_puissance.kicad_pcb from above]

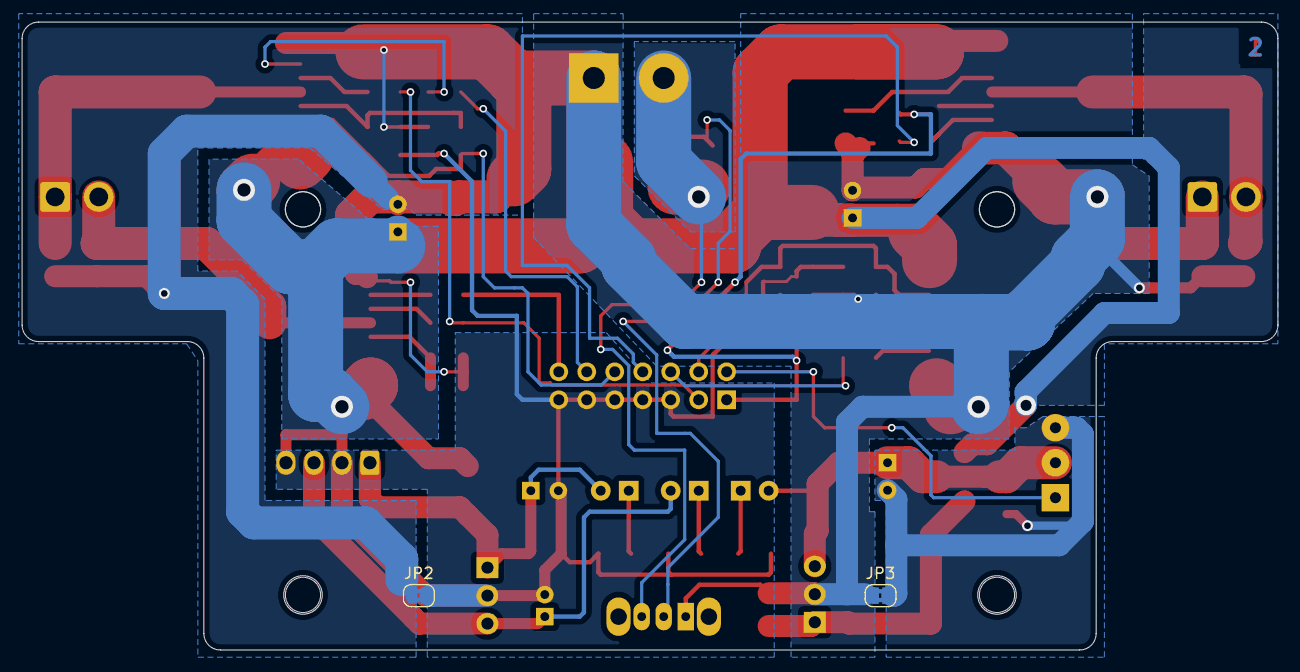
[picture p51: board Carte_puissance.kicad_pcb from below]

Board: 2 copper layers, 114.0 x 57.0 mm, 63 parts (2 on the bottom side), 38 nets.

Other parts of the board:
REF1: OSHW-Logo2_9.8x8mm_SilkScreen
REF2: LOGO; insa-image

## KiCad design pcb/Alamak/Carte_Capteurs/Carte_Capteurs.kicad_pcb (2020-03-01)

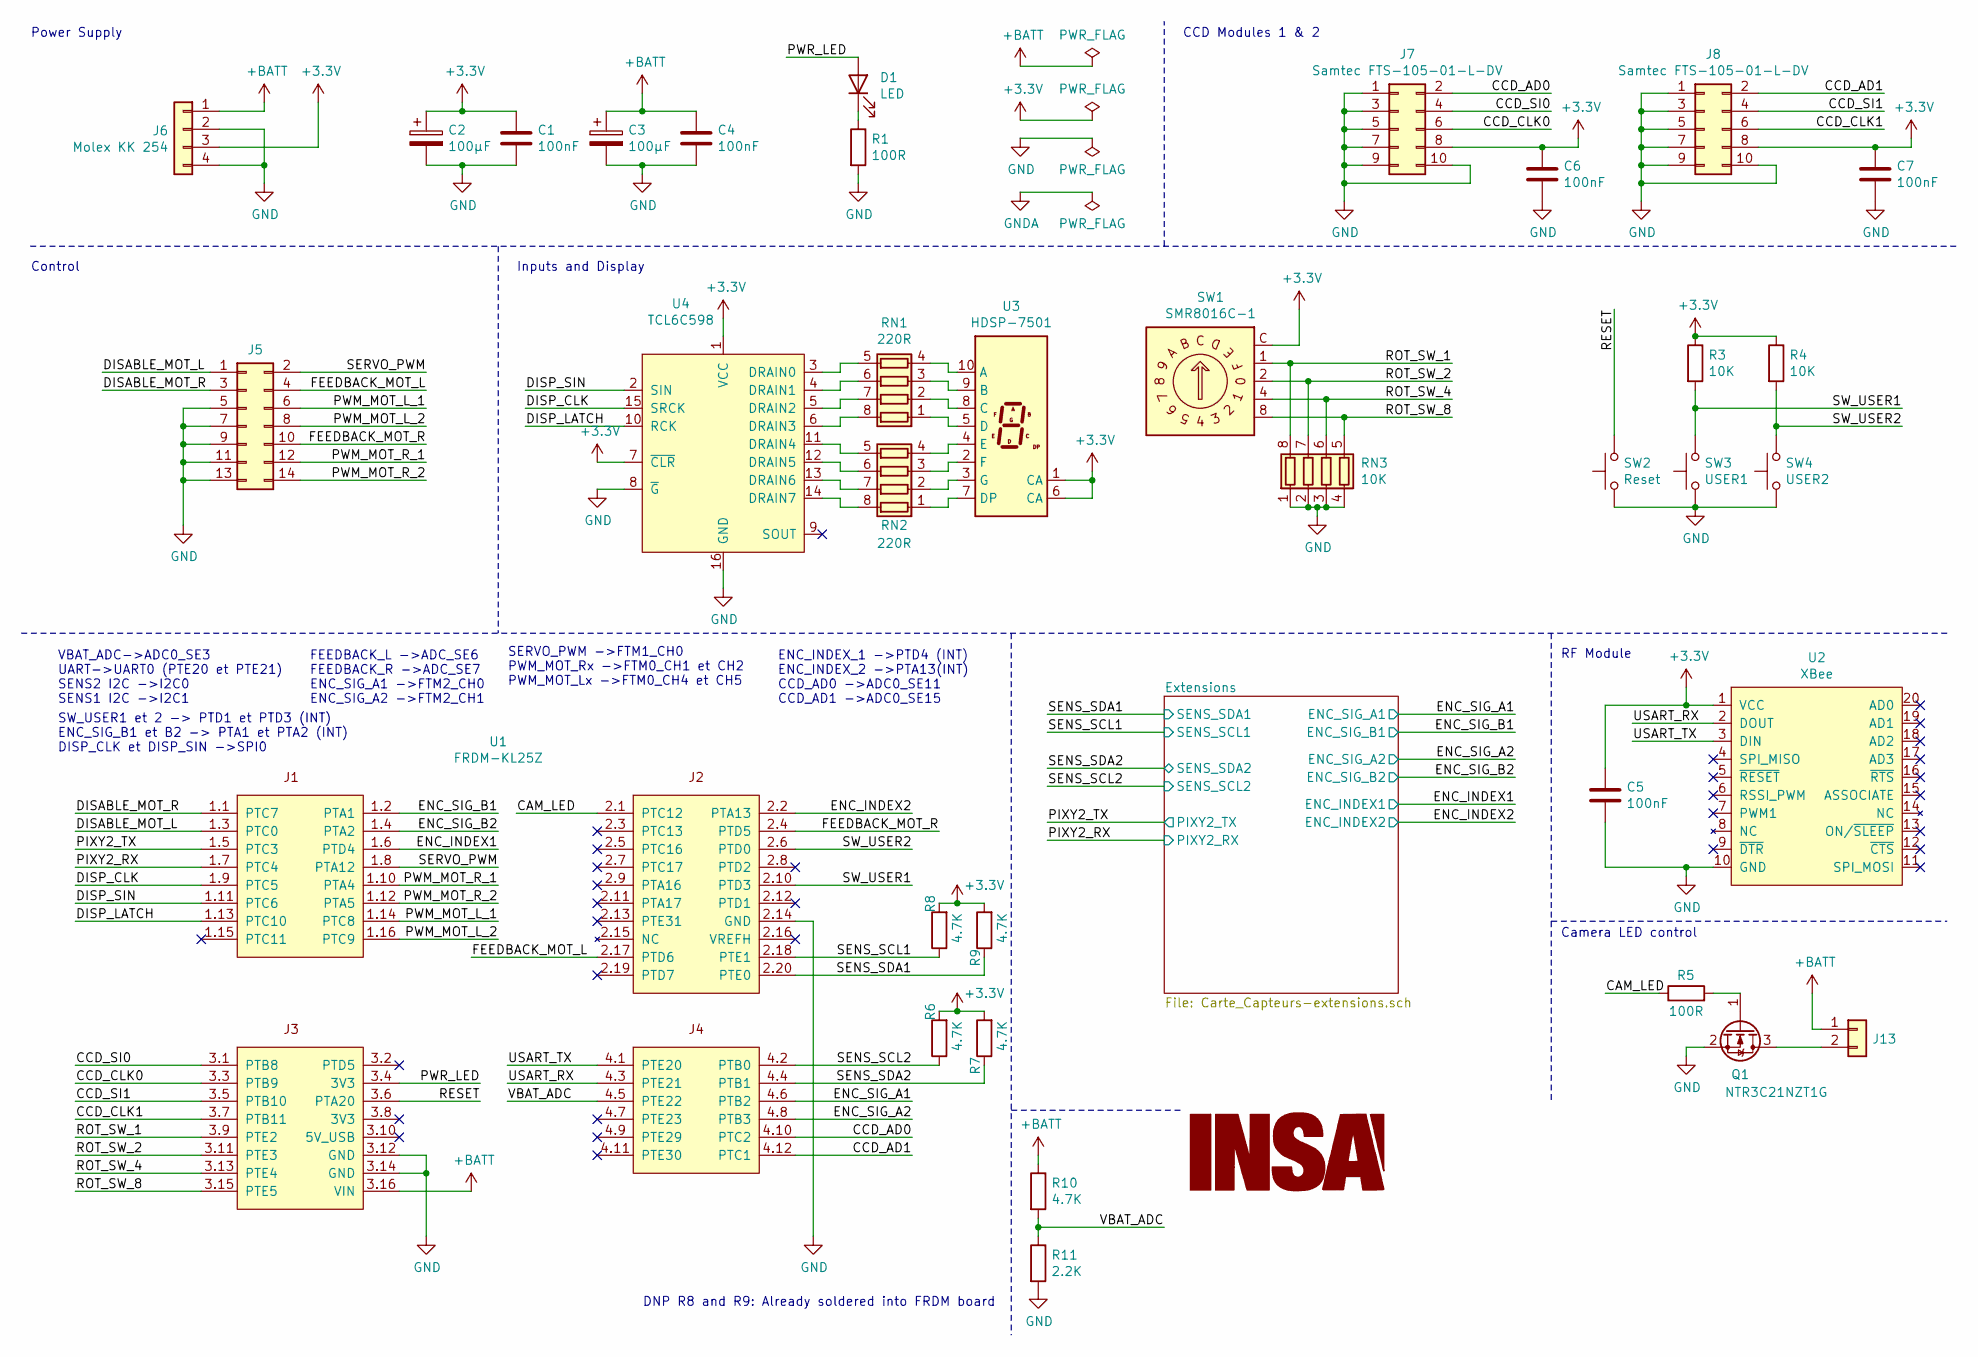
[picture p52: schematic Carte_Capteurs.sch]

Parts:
C1, C4, C5, C6, C7: 100nF; C_1206_3216Metric_Pad1.42x1.75mm_HandSolder
C2, C3: 100µF; CP_Radial_D6.3mm_P2.50mm
D1: LED; LED_D3.0mm
J5: Conn_02x07_Odd_Even; PinHeader_2x07_P2.54mm_Vertical
J6: Molex KK 254; Molex_KK-254_AE-6410-04A_1x04_P2.54mm_Vertical
J7, J8: Samtec FTS-105-01-L-DV; PinHeader_2x05_P1.27mm_Vertical
J13: Conn_01x02; PinHeader_1x02_P2.54mm_Vertical
Logo1: LOGO; insa-image
Q1: NTR3C21NZT1G; SOT-23
R1, R5: 100R; R_1206_3216Metric_Pad1.42x1.75mm_HandSolder
R3, R4: 10K; R_1206_3216Metric_Pad1.42x1.75mm_HandSolder
R6, R7, R8, R9, R10: 4.7K; R_1206_3216Metric_Pad1.42x1.75mm_HandSolder
R11: 2.2K; R_1206_3216Metric_Pad1.42x1.75mm_HandSolder
RN1, RN2: 220R; R_Array_Convex_4x0603
RN3: 10K; R_Array_Convex_4x0603
SW1: SMR8016C-1; Nidec_Copal_SMR-8016C
SW2: Reset; SW_PUSH_6mm_H4.3mm
SW3: USER1; SW_PUSH_6mm_H4.3mm
SW4: USER2; SW_PUSH_6mm_H4.3mm
U1: FRDM-KL25Z
U2: XBee; Xbee3
U3: HDSP-7501; HDSP-A151
U4: TCL6C598; TSSOP-16_4.4x5mm_P0.65mm

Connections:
+3V3: C1.1, C2.1, C5.1, C6.1, C7.1, J6.3, J7.8, J8.8, R3.1, R4.1, R6.2, R7.2, R8.2, R9.2, SW1.C, U2.1 (VCC), U3.1 (CA), U3.6 (CA), U4.1 (VCC), U4.7 (~CLR); also elsewhere on the board
+BATT: C3.1, C4.1, J6.1, J13.1, R10.1, U1.3.16 (VIN); also elsewhere on the board
/CAM_LED: R5.1, U1.2.1 (PTC12)
/CCD_AD0: J7.2, U1.4.10 (PTC2)
/CCD_AD1: J8.2, U1.4.12 (PTC1)
/CCD_CLK0: J7.6, U1.3.3 (PTB9)
/CCD_CLK1: J8.6, U1.3.7 (PTB11)
/CCD_SI0: J7.4, U1.3.1 (PTB8)
/CCD_SI1: J8.4, U1.3.5 (PTB10)
/DISABLE_MOT_L: J5.1, U1.1.3 (PTC0)
/DISABLE_MOT_R: J5.3, U1.1.1 (PTC7)
/DISP_CLK: U1.1.9 (PTC5), U4.15 (SRCK)
/DISP_LATCH: U1.1.13 (PTC10), U4.10 (RCK)
/DISP_SIN: U1.1.11 (PTC6), U4.2 (SIN)
/ENC_INDEX1: U1.1.6 (PTD4); also elsewhere on the board
/ENC_INDEX2: U1.2.2 (PTA13); also elsewhere on the board
/ENC_SIG_A1: U1.4.6 (PTB2); also elsewhere on the board
/ENC_SIG_A2: U1.4.8 (PTB3); also elsewhere on the board
/ENC_SIG_B1: U1.1.2 (PTA1); also elsewhere on the board
/ENC_SIG_B2: U1.1.4 (PTA2); also elsewhere on the board
/FEEDBACK_MOT_L: J5.4, U1.2.17 (PTD6)
/FEEDBACK_MOT_R: J5.10, U1.2.4 (PTD5)
/PIXY2_RX: U1.1.7 (PTC4); also elsewhere on the board
/PIXY2_TX: U1.1.5 (PTC3); also elsewhere on the board
/PWM_MOT_L_1: J5.6, U1.1.14 (PTC8)
/PWM_MOT_L_2: J5.8, U1.1.16 (PTC9)
/PWM_MOT_R_1: J5.12, U1.1.10 (PTA4)
/PWM_MOT_R_2: J5.14, U1.1.12 (PTA5)
/PWR_LED: D1.2 (A), U1.3.4 (3V3)
/RESET: SW2.2, U1.3.6 (PTA20)
/ROT_SW_1: RN3.8 (R1.2), SW1.1, U1.3.9 (PTE2)
/ROT_SW_2: RN3.7 (R2.2), SW1.2, U1.3.11 (PTE3)
/ROT_SW_4: RN3.6 (R3.2), SW1.4, U1.3.13 (PTE4)
/ROT_SW_8: RN3.5 (R4.2), SW1.8, U1.3.15 (PTE5)
/SENS_SCL1: R8.1, U1.2.18 (PTE1); also elsewhere on the board
/SENS_SCL2: R6.1, U1.4.2 (PTB0); also elsewhere on the board
/SENS_SDA1: R9.1, U1.2.20 (PTE0); also elsewhere on the board
/SENS_SDA2: R7.1, U1.4.4 (PTB1); also elsewhere on the board
/SERVO_PWM: J5.2, U1.1.8 (PTA12)
/SW_USER1: R3.2, SW3.2, U1.2.10 (PTD3)
/SW_USER2: R4.2, SW4.2, U1.2.6 (PTD0)
/USART_RX: U1.4.3 (PTE21), U2.2 (DOUT)
/USART_TX: U1.4.1 (PTE20), U2.3 (DIN)
/VBAT_ADC: R10.2, R11.1, U1.4.5 (PTE22)
GND: C1.2, C2.2, C3.2, C4.2, C5.2, C6.2, C7.2, J5.5, J5.7, J5.9, J5.11, J5.13, J6.2, J6.4, J7.1, J7.3, J7.5, J7.7, J7.9, J7.10, J8.1, J8.3, J8.5, J8.7, J8.9, J8.10, Q1.2 (S), R1.2, R11.2, RN3.1 (R1.1), RN3.2 (R2.1), RN3.3 (R3.1), RN3.4 (R4.1), SW2.1, SW3.1, SW4.1, U1.2.14 (GND), U1.3.12 (GND), U1.3.14 (GND), U2.10 (GND), U4.8 (~G), U4.16 (GND); also elsewhere on the board
unnamed: D1.1 (K), R1.1
unnamed: J13.2, Q1.3 (D)
unnamed: Q1.1 (G), R5.2
unnamed: RN1.1 (R1.1), U3.5 (D)
unnamed: RN1.2 (R2.1), U3.8 (C)
unnamed: RN1.3 (R3.1), U3.9 (B)
unnamed: RN1.4 (R4.1), U3.10 (A)
unnamed: RN1.5 (R4.2), U4.3 (DRAIN0)
unnamed: RN1.6 (R3.2), U4.4 (DRAIN1)
unnamed: RN1.7 (R2.2), U4.5 (DRAIN2)
unnamed: RN1.8 (R1.2), U4.6 (DRAIN3)
unnamed: RN2.1 (R1.1), U3.7 (DP)
unnamed: RN2.2 (R2.1), U3.3 (G)
unnamed: RN2.3 (R3.1), U3.2 (F)
unnamed: RN2.4 (R4.1), U3.4 (E)
unnamed: RN2.5 (R4.2), U4.11 (DRAIN4)
unnamed: RN2.6 (R3.2), U4.12 (DRAIN5)
unnamed: RN2.7 (R2.2), U4.13 (DRAIN6)
unnamed: RN2.8 (R1.2), U4.14 (DRAIN7)

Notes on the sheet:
Power Supply
Control
Inputs and Display
CCD Modules 1 & 2
RF Module
Camera LED control
DNP R8 and R9: Already soldered into FRDM board
VBAT_ADC->ADC0_SE3 UART->UART0 (PTE20 et PTE21) SENS2 I2C ->I2C0 SENS1 I2C ->I2C1
FEEDBACK_L ->ADC_SE6 FEEDBACK_R ->ADC_SE7 ENC_SIG_A1 ->FTM2_CH0 ENC_SIG_A2 ->FTM2_CH1
SERVO_PWM ->FTM1_CH0 PWM_MOT_Rx ->FTM0_CH1 et CH2 PWM_MOT_Lx ->FTM0_CH4 et CH5
ENC_INDEX_1 ->PTD4 (INT) ENC_INDEX_2 ->PTA13(INT) CCD_AD0 ->ADC0_SE11 CCD_AD1 ->ADC0_SE15
SW_USER1 et 2 -> PTD1 et PTD3 (INT) ENC_SIG_B1 et B2 -> PTA1 et PTA2 (INT) DISP_CLK et DISP_SIN ->SPI0

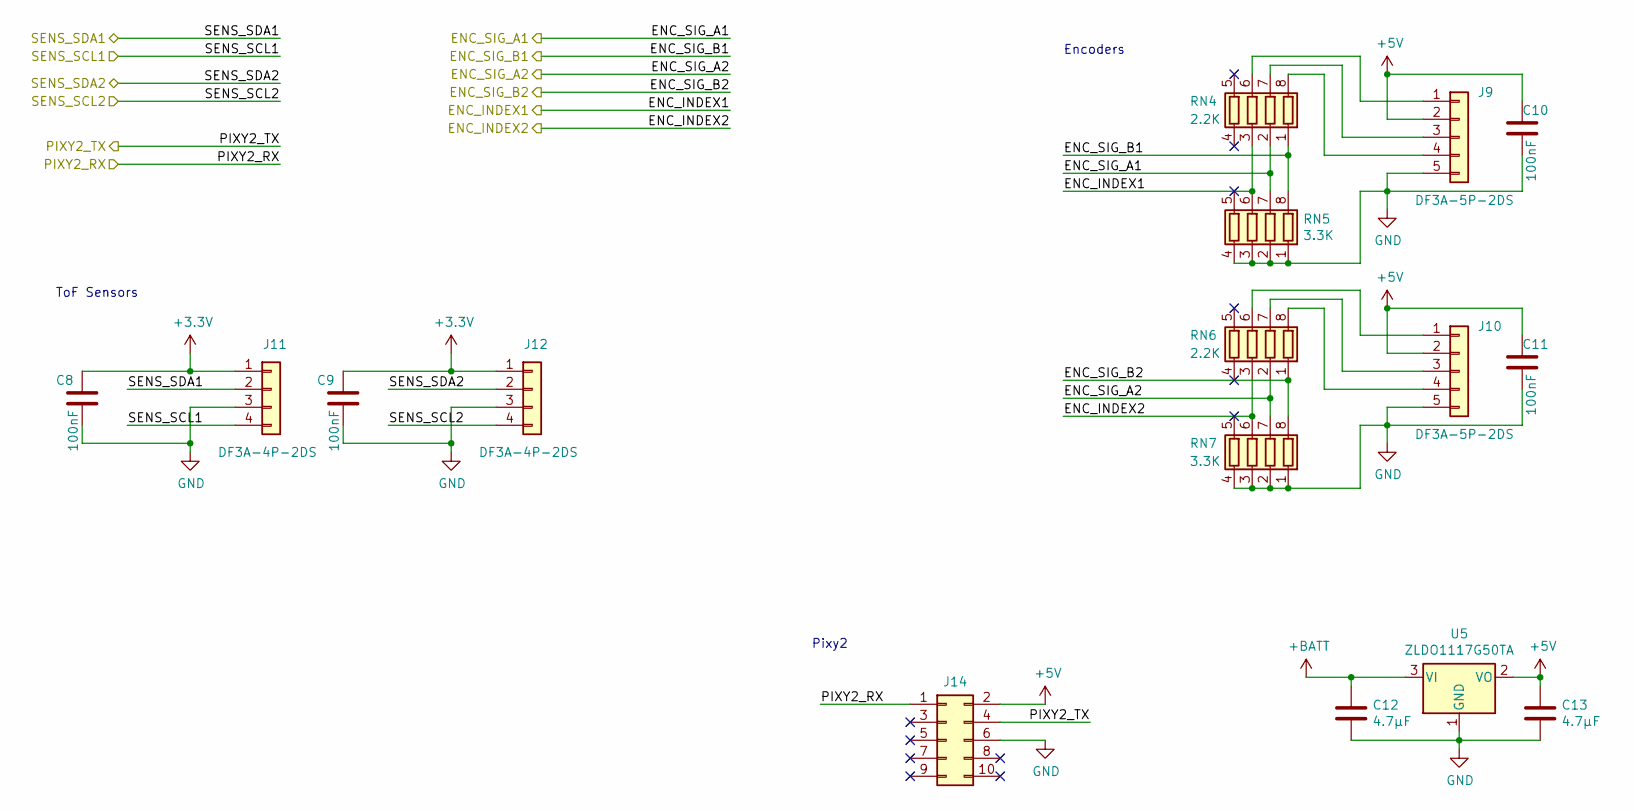
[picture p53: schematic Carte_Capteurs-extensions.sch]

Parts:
C8, C9, C10, C11: 100nF; C_1206_3216Metric_Pad1.42x1.75mm_HandSolder
C12, C13: 4.7µF; C_1206_3216Metric_Pad1.42x1.75mm_HandSolder
J9, J10: DF3A-5P-2DS
J11, J12: DF3A-4P-2DS
J14: Conn_02x05_Odd_Even; Multicomp_MC9A12-1034_2x05_P2.54mm_Vertical
RN4, RN6: 2.2K; R_Array_Convex_4x0603
RN5, RN7: 3.3K; R_Array_Convex_4x0603
U5: ZLDO1117G50TA; SOT-223-3_TabPin2

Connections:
+3V3: C8.1, C9.1, J11.1, J12.1; also elsewhere on the board
+5V: C10.1, C11.1, C13.1, J9.2, J10.2, J14.2, U5.2 (VO)
+BATT: C12.1, U5.3 (VI); also elsewhere on the board
/ENC_INDEX1: RN4.3 (R3.1), RN5.6 (R3.2); also elsewhere on the board
/ENC_INDEX2: RN6.3 (R3.1), RN7.6 (R3.2); also elsewhere on the board
/ENC_SIG_A1: RN4.2 (R2.1), RN5.7 (R2.2); also elsewhere on the board
/ENC_SIG_A2: RN6.2 (R2.1), RN7.7 (R2.2); also elsewhere on the board
/ENC_SIG_B1: RN4.1 (R1.1), RN5.8 (R1.2); also elsewhere on the board
/ENC_SIG_B2: RN6.1 (R1.1), RN7.8 (R1.2); also elsewhere on the board
/PIXY2_RX: J14.1; also elsewhere on the board
/PIXY2_TX: J14.4; also elsewhere on the board
/SENS_SCL1: J11.4; also elsewhere on the board
/SENS_SCL2: J12.4; also elsewhere on the board
/SENS_SDA1: J11.2; also elsewhere on the board
/SENS_SDA2: J12.2; also elsewhere on the board
GND: C8.2, C9.2, C10.2, C11.2, C12.2, C13.2, J9.5, J10.5, J11.3, J12.3, J14.6, RN5.1 (R1.1), RN5.2 (R2.1), RN5.3 (R3.1), RN5.4 (R4.1), RN7.1 (R1.1), RN7.2 (R2.1), RN7.3 (R3.1), RN7.4 (R4.1), U5.1 (GND); also elsewhere on the board
unnamed: J9.1, RN4.6 (R3.2)
unnamed: J9.3, RN4.7 (R2.2)
unnamed: J9.4, RN4.8 (R1.2)
unnamed: J10.1, RN6.6 (R3.2)
unnamed: J10.3, RN6.7 (R2.2)
unnamed: J10.4, RN6.8 (R1.2)

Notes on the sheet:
ToF Sensors
Encoders
Pixy2

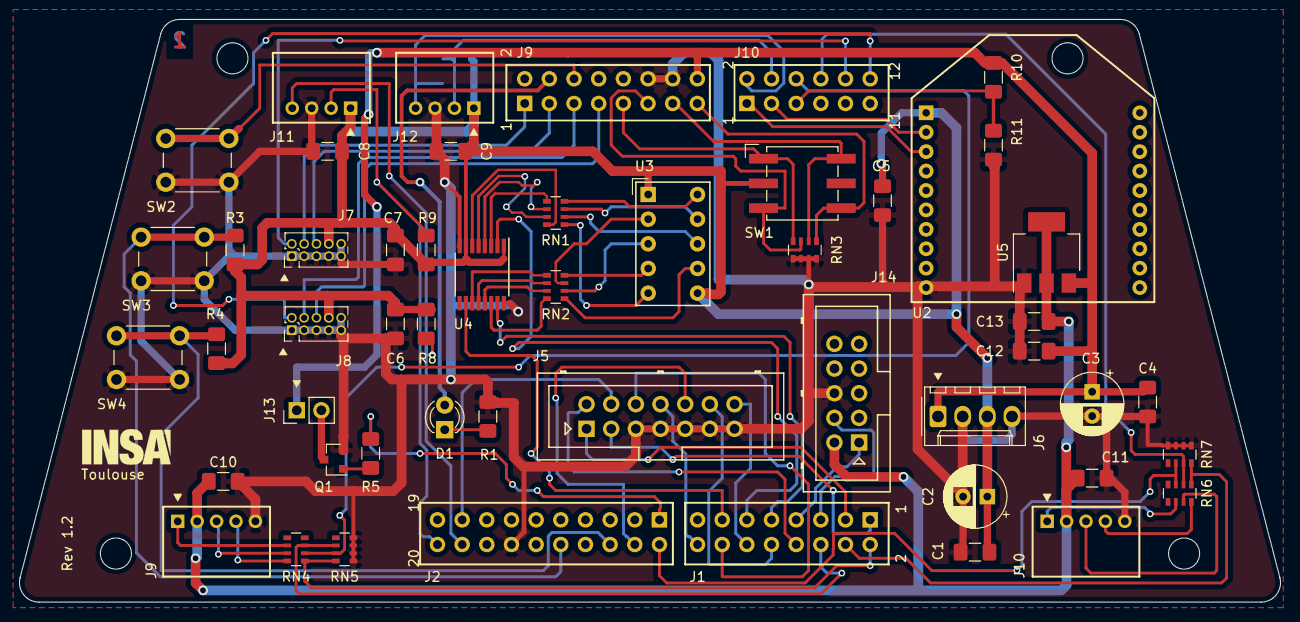
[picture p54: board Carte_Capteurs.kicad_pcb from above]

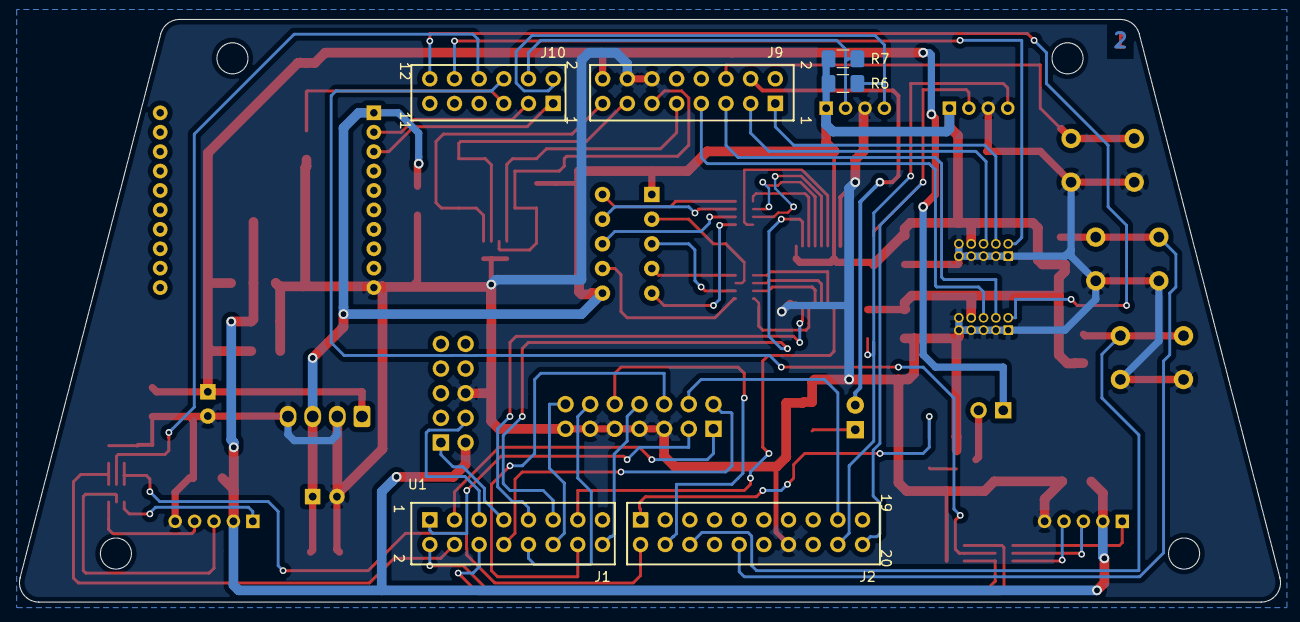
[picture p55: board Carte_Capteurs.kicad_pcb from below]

Board: 2 copper layers, 129.9 x 60.0 mm, 52 parts (3 on the bottom side), 71 nets.

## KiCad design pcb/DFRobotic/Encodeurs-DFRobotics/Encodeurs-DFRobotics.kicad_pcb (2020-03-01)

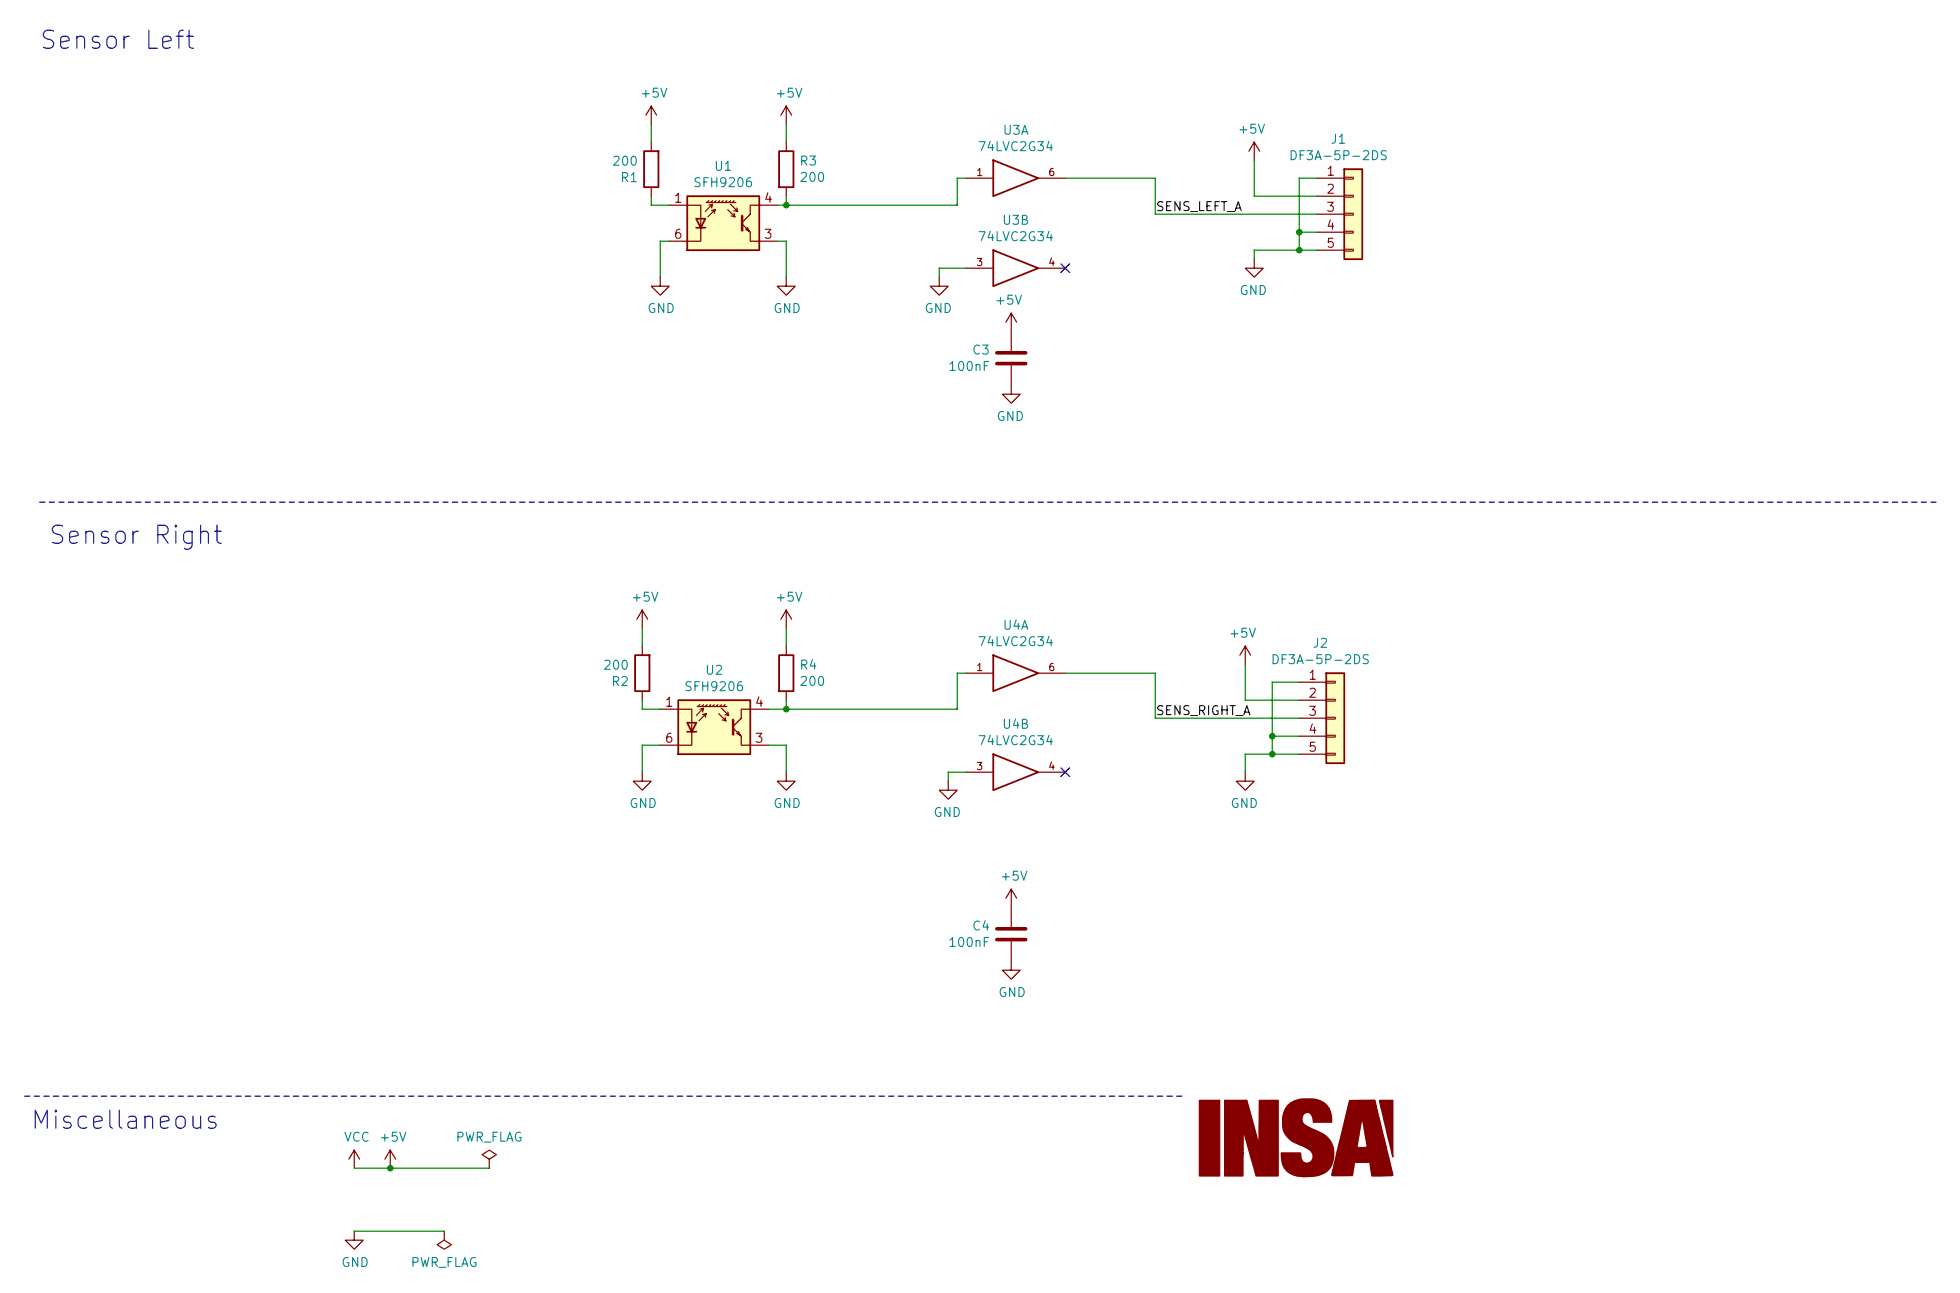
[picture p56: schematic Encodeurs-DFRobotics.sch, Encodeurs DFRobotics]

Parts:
C3, C4: 100nF; C_0805_2012Metric_Pad1.15x1.40mm_HandSolder
G1: LOGO
J1, J2: DF3A-5P-2DS
R1, R2, R3, R4: 200; R_0805_2012Metric_Pad1.15x1.40mm_HandSolder
U1, U2: SFH9206; Osram_SFH9x0x
U3, U4: 74LVC2G34; SOT-363_SC-70-6_Handsoldering

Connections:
+5V: C3.1, C4.1, J1.2, J2.2, R1.2, R2.2, R3.1, R4.1, U3.5 (VCC), U4.5 (VCC)
/SENS_LEFT_A: J1.3, U3.6
/SENS_RIGHT_A: J2.3, U4.6
GND: C3.2, C4.2, J1.1, J1.4, J1.5, J2.1, J2.4, J2.5, U1.3 (E), U1.6 (K), U2.3 (E), U2.6 (K), U3.2 (GND), U3.3, U4.2 (GND), U4.3
unnamed: R1.1, U1.1 (A)
unnamed: R2.1, U2.1 (A)
unnamed: R3.2, U1.4 (C), U3.1
unnamed: R4.2, U2.4 (C), U4.1

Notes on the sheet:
Sensor Left
Sensor Right
Miscellaneous

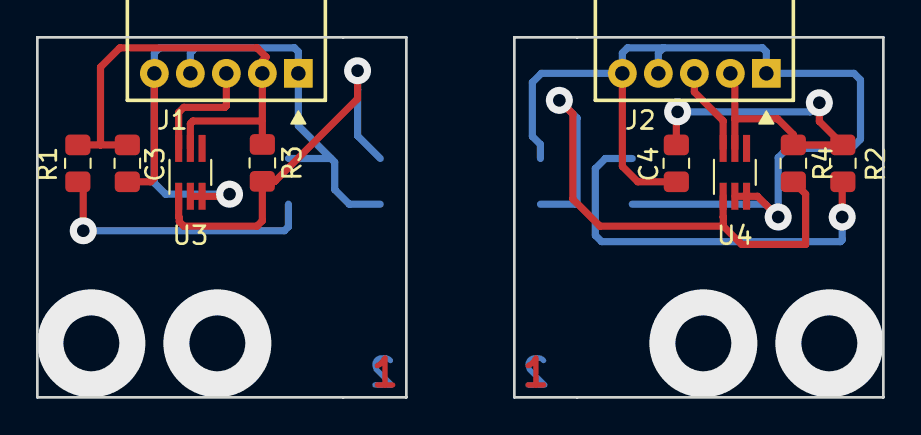
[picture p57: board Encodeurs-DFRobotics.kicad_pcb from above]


Board: 2 copper layers, 47.0 x 20.0 mm, 12 parts (2 on the bottom side), 8 nets.

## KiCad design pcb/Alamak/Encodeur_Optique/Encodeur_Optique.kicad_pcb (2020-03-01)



Board: 2 copper layers, 50.0 x 28.5 mm, 20 parts (2 on the bottom side), 12 nets.

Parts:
C1D1, C1G1, C2D1, C2G1: 100nF; C_1206_3216Metric_Pad1.42x1.75mm_HandSolder
D1D1, D1G1: Led Verte; LED_1206_3216Metric_Pad1.42x1.75mm_HandSolder
D2D1, D2G1: Led Rouge; LED_1206_3216Metric_Pad1.42x1.75mm_HandSolder
J1D1, J1G1: Conn_01x04; PinHeader_1x04_P2.54mm_Horizontal
R1D1, R1G1, R2D1, R2G1, R3D1, R3G1: R; R_1206_3216Metric_Pad1.42x1.75mm_HandSolder
U1D1, U1G1: GP1A52LRJ00F
U2D1, U2G1: 74LVC1G17; SOT-553

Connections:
/OUT_D: J1D1.3, R3D1.1, U2D1.4
/OUT_G: J1G1.3, R3G1.1, U2G1.4
GND: C1D1.2, C1G1.2, C2D1.2, C2G1.2, D1D1.1, D1G1.1, D2D1.1, D2G1.1, J1D1.2, J1G1.2, U1D1.2, U1D1.5, U1G1.2, U1G1.5, U2D1.3, U2G1.3
unnamed: D1D1.2, R2D1.2
unnamed: D1G1.2, R2G1.2
unnamed: D2D1.2, R3D1.2
unnamed: D2G1.2, R3G1.2
unnamed: R1D1.2, U1D1.1
unnamed: R1G1.2, U1G1.1
unnamed: U1D1.4, U2D1.2
unnamed: U1G1.4, U2G1.2
VCC: C1D1.1, C1G1.1, C2D1.1, C2G1.1, J1D1.1, J1G1.1, R1D1.1, R1G1.1, R2D1.1, R2G1.1, U1D1.3, U1G1.3, U2D1.5, U2G1.5

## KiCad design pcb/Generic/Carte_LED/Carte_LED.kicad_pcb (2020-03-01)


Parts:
C1, C2: 4.7µF; C_1206_3216Metric_Pad1.42x1.75mm_HandSolder
D1, D2, D3, D4, D5, D6, D7, D8, D9, D10, D11, D12: VLCS5830; LED_D5.0mm_Clear
G1: LOGO; insa-image
H1, H2: MountingHole; MountingHole_2.7mm_M2.5
J1: Conn_01x02; PinHeader_1x02_P2.54mm_Vertical
JP1, JP2: SolderJumper_2_Open; SolderJumper-2_P1.3mm_Open_RoundedPad1.0x1.5mm
R1, R2, R3, R4, R5, R6: 0R; R_Axial_DIN0309_L9.0mm_D3.2mm_P2.54mm_Vertical
U1: ZLDO1117G50TA; SOT-223-3_TabPin2

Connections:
+5V: JP1.2 (B), JP2.2 (B), R1.2, R2.2, R3.2, R4.2, R5.2, R6.2
+BATT: C1.1, J1.2, JP1.1 (A), U1.3 (VI)
GND: C1.2, C2.2, D2.1 (K), D4.1 (K), D6.1 (K), D8.1 (K), D10.1 (K), D12.1 (K), J1.1, U1.1 (GND)
unnamed: C2.1, JP2.1 (A), U1.2 (VO)
unnamed: D1.1 (K), D2.2 (A)
unnamed: D1.2 (A), R1.1
unnamed: D3.1 (K), D4.2 (A)
unnamed: D3.2 (A), R2.1
unnamed: D5.1 (K), D6.2 (A)
unnamed: D5.2 (A), R3.1
unnamed: D7.1 (K), D8.2 (A)
unnamed: D7.2 (A), R4.1
unnamed: D9.2 (A), R5.1
unnamed: D9.1 (K), D10.2 (A)
unnamed: D11.1 (K), D12.2 (A)
unnamed: D11.2 (A), R6.1

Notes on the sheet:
VLCS5B30: 2.5V@35mA



Board: 2 copper layers, 100.0 x 38.0 mm, 27 parts (5 on the bottom side), 16 nets.

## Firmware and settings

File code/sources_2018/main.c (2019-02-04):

/*
 * FRDM-KL25 Freedom Board NXP Cup Minimal Program
 * (c) THD Technische Hochschule Deggendorf
 * (c) DIT Deggendorf Institute of Technology
 * Version 2.1, 09.01.2018
 * Change: ported to NXP Cup and Alamank Car
 */

#include "derivative.h" /* include peripheral declarations */

// Define threshold for Camera Black Line recognition
#define THRESHOLD				150			// Difference between black and white

// Defines for Direction PD Servo Control Loop
#define KP						40			// Proportional coefficient
#define KDP						45			// Differential coefficient

// Defines for LineScan Camera
#define TAOS_DELAY				asm ("nop")				// minimal delay time
#define	TAOS_SI_HIGH			GPIOB_PDOR |= (1<<8)	// SI on PTB8
#define	TAOS_SI_LOW				GPIOB_PDOR &= ~(1<<8)	// SI on PTB8
#define	TAOS_CLK_HIGH			GPIOB_PDOR |= (1<<9)	// CLK on PTB9
#define	TAOS_CLK_LOW			GPIOB_PDOR &= ~(1<<9)	// CLK on PTB9

// Function declaration
void ImageCapture(void);
int abs (int);

// Variable declaration
int i;										// counter for loops
int temp_reg;								// temporary register
int ImageData [128];						// array to store the LineScan image
int ImageDataDifference [128];				// array to store the PineScan pixel difference
int BlackLineRight;							// position of the black line on the right side
int BlackLineLeft;							// position of the black line on the left side
int RoadMiddle = 0;							// calculated middle of the road
int diff = 0;								// actual difference from line middle position
int diff_old = 0;							// previous difference from line middle position
int servo_position = 0;						// actual position of the servo relative to middle
int servo_position_old = 0;					// old servo position
int CompareData;							// set data for comparison to find max

// Main program
int main(void){
	
	// configure clock to 48 MHz from a 8 MHz crystal
	MCG_C2 = (MCG_C2_RANGE0(1) | MCG_C2_EREFS0_MASK); 	// configure the oscillator settings
	MCG_C1 = (MCG_C1_CLKS(2) | MCG_C1_FRDIV(3));		// divider for 8 MHz clock	
	for (i = 0 ; i < 24000 ; i++)						// wait for OSCINIT to set
	// now in FBE mode
	MCG_C6 |= MCG_C6_CME0_MASK;		// enable the clock monitor
	MCG_C5 |= MCG_C5_PRDIV0(1); 	// set PLL ref divider to divide by 2
	temp_reg = MCG_C6; 				// store present C6 value (as CME0 bit was previously set)
	temp_reg &= ~MCG_C6_VDIV0_MASK; // clear VDIV settings
	temp_reg |= MCG_C6_PLLS_MASK | MCG_C6_VDIV0(0); 	// write new VDIV and enable PLL
	MCG_C6 = temp_reg; 				// update MCG_C6		
	for (i = 0 ; i < 4000 ; i++) 	// wait for PLLST status bit to set
	// now in PBE mode
	SIM_CLKDIV1 = (SIM_CLKDIV1_OUTDIV1(1) | SIM_CLKDIV1_OUTDIV4(1));	// core clock, bus clock div by 2	
	MCG_C1 &= ~MCG_C1_CLKS_MASK;	// switch CLKS mux to select the PLL as MCGCLKOUT	
	for (i = 0 ; i < 2000 ; i++)	// Wait for clock status bits to update
	// now in PEE mode, core and system clock 48 MHz, bus and flash clock 24 MHz

	// turn on all port clocks
	SIM_SCGC5 = SIM_SCGC5_PORTA_MASK | SIM_SCGC5_PORTB_MASK | SIM_SCGC5_PORTC_MASK | SIM_SCGC5_PORTD_MASK | SIM_SCGC5_PORTE_MASK;
	
	// turn on all UART clocks - not needed in this project
	SIM_SCGC4 = SIM_SCGC4_UART0_MASK | SIM_SCGC4_UART1_MASK | SIM_SCGC4_UART2_MASK;
	
	// turn on all TPM clocks
	SIM_SCGC6 |= SIM_SCGC6_TPM0_MASK | SIM_SCGC6_TPM1_MASK | SIM_SCGC6_TPM2_MASK;

	// turn on ADC0 clock
	SIM_SCGC6 |= SIM_SCGC6_ADC0_MASK;

	// set ADC inputs to ADC inputs
	PORTC_PCR2  |= PORT_PCR_MUX(0);		// Camera 1 PTC2 ADC0_SE11
	
	// set GPIOs to GPIO function
	PORTC_PCR0  |= PORT_PCR_MUX(1);	// PTC0 Push Button S2
	PORTB_PCR18 |= PORT_PCR_MUX(1);	// PTB18 LED red
	PORTB_PCR19 |= PORT_PCR_MUX(1);	// PTB19 LED green
	PORTD_PCR1  |= PORT_PCR_MUX(1);	// PTD1  LED blue
	PORTB_PCR8  |= PORT_PCR_MUX(1);	// PTB8 Camera SI
	PORTB_PCR9  |= PORT_PCR_MUX(1);	// PTB9 Camera Clock
	PORTA_PCR4  = 0;				// Set PTA4 Pin Control Register to Zero
	PORTA_PCR4  |= PORT_PCR_MUX(3);	// PTA4 Motor 1 In 1 (speed) PTA4 TPM0_CH1
	PORTA_PCR5  |= PORT_PCR_MUX(1);	// PTA5 Motor 1 In 2 (direction)
	PORTC_PCR8  |= PORT_PCR_MUX(1);	// PTC8 Motor 2 In 1 (direction)
	PORTC_PCR9  |= PORT_PCR_MUX(3);	// PTC9 Motor 2 In 2 (speed) PTC8 TPM0_CH5
	
	// set GPIO outputs to outputs
	GPIOB_PDDR |= (1<<18);			// PTB18 LED red
	GPIOB_PDDR |= (1<<19);			// PTB19 LED green
	GPIOD_PDDR |= (1<<1);			// PTD1  LED blue
	GPIOB_PDDR |= (1<<8);			// PTB8 Camera SI
	GPIOB_PDDR |= (1<<9);			// PTB9 Camera Clock
	GPIOA_PDDR |= (1<<4);			// PTA4 Motor 1 In 1
	GPIOA_PDDR |= (1<<5);			// PTA5 Motor 1 In 2 (direction)
	GPIOC_PDDR |= (1<<8);			// PTC9 Motor 2 In 1 (direction)
	GPIOC_PDDR |= (1<<9);			// PTC9 Motor 2 In 2 
	
	// all LEDs off
	GPIOB_PDOR |= GPIO_PDOR_PDO(1<<18);   // red LED off
	GPIOB_PDOR |= GPIO_PDOR_PDO(1<<19);   // green LED off
	GPIOD_PDOR |= GPIO_PDOR_PDO(1<<1);    // blue LED off	
	
	// GPIOB_PDOR &= ~GPIO_PDOR_PDO(1<<18);  // red LED on
	// GPIOB_PDOR &= ~GPIO_PDOR_PDO(1<<19);  // green LED on
	// GPIOD_PDOR &= ~GPIO_PDOR_PDO(1<<1);   // blue LED on	
			
	// set GPIO input to input
	GPIOC_PDDR &= ~ (1<<0);			// PTC0 Push Button S2

	// set PWM outputs
	PORTA_PCR12 |= PORT_PCR_MUX(3);	// Servo Motor 1 Out  PTA12 TPM1_CH0
	
	// configure TPM clock source to be 48 MHz
	SIM_SOPT2 |= SIM_SOPT2_TPMSRC(1);		// MCGFLLCLK clock or MCGPLLCLK/2
	SIM_SOPT2 |= SIM_SOPT2_PLLFLLSEL_MASK;	// use MCGPLLCLK/2 clock when running from 8 MHz and PLL
		
	// set TPM prescaler before enabling the timer
	TPM0_SC |= 3;					// prescaler for TPM0 (Motor) is 8
	TPM1_SC |= 3;					// prescaler for TPM1 (Servo) is 8
	
	// TPM modulo register, set frequency
	TPM0_MOD = 600;					// modulo TPM0 (Motor), periode = 0.10 ms (10000 Hz)
	TPM1_MOD = 60000;				// modulo TPM0 (Servo), periode = 10 ms (100 Hz)
	
	// set TPM clock mode to enable timer
	TPM0_SC |= TPM_SC_CMOD(1);		// enable TPM0 (Motor)
	TPM1_SC |= TPM_SC_CMOD(1);		// enable TPM1 (Servo)
	
	// configure TPM channel outputs high-true pulses
	TPM0_C1SC = 0x28;				// TPM0 channel1 Motor 1 In 1 speed left
	TPM0_C5SC = 0x28;				// TPM0 channel5 Motor 2 In 2 speed right
	TPM1_C0SC = 0x28;				// TPM1 channel0 Servo 1
	
	// TPM channel value registers, sets duty cycle
	TPM1_C0V = 8200;				// TPM1 channel0 Servo 1 ca. 1.5 ms (middle)
	
    // initial configuration of motors
	TPM0_C1V = 10;					// TPM0 channel1 left Motor 1 In 1 slow forward
	TPM0_C5V = 10;					// TPM0 channel5 right Motor 2 In 2 slow forward
	GPIOA_PDOR &= ~(1<<5);			// Set PTA5 left Motor 1 In 2 forward
	GPIOC_PDOR &= ~(1<<8);			// Set PTC8 right Motor 2 In 1 forward
	
    // configure interrupts in TPM0
	TPM1_SC |= TPM_SC_TOIE_MASK;	// enable overflow interrupt in TPM1 (10 ms rate)
	
	// ADC0 clock configuration
	ADC0_CFG1 |= 0x01;				// clock is bus clock divided by 2 = 12 MHz
	
	// ADC0 resolution    
	ADC0_CFG1 |= 0x08;				// resolution 10 bit, max. value is 1023

	// ADC0 conversion mode
	ADC0_SC3 = 0x00;				// single conversion mode
	    
    // enable interrupts 18 (TPM = FTM1)  in NVIC, no interrupt levels
    NVIC_ICPR |= (1 << 18);			// clear pending interrupt 18
    NVIC_ISER |= (1 << 18);			// enable interrupt 18
    
    // enable interrupts globally
    asm (" CPSIE i ");				// enable interrupts on core level
    
    // Main loop
	for(;;) {						// endless loop

		// do nothing
		
	}								// end of endless loop	
	return 0;
}

void FTM1_IRQHandler()				// TPM1 ISR
{
	TPM1_SC |= 0x80;							// clear TPM1 ISR flag
	
	GPIOB_PDOR &= ~GPIO_PDOR_PDO(1<<18);  // red LED on
	
	// Capture Line Scan Image
	ImageCapture();								// capture LineScan image
	
	// Find black line on the right side
	for(i=64;i<127;i++)							// calculate difference between the pixels
	{
		ImageDataDifference[i] = abs (ImageData[i] - ImageData[i+1]);
	}
	CompareData = THRESHOLD;					// threshold
	BlackLineRight = 126;
	for(i=64;i<127;i++)
	{
	   	if (ImageDataDifference[i] > CompareData)
	   	{
	   		CompareData = ImageDataDifference[i];
	   		BlackLineRight = i;
	   	}
	}
	
	// Find black line on the left side
	for(i=64;i>0;i--)							// calculate difference between the pixels
	{
		ImageDataDifference[i] = abs (ImageData[i] - ImageData[i-1]);
	}
	CompareData = THRESHOLD;					// threshold
	BlackLineLeft = 1;
	for(i=64;i>2;i--)							// only down to pixel 3, not 1
	{
	   	if (ImageDataDifference[i] > CompareData)
	   	{
	   		CompareData = ImageDataDifference[i];
	   		BlackLineLeft = i;
	   	}
	}
	
	// Find middle of the road, 64 for strait road
	RoadMiddle = (BlackLineLeft + BlackLineRight)/2;
	
	// if a line is only on the the left side
	if (BlackLineRight > 124)
	{
		RoadMiddle = BlackLineLeft + 50;
	}
	// if a line is only on the the right side
	if (BlackLineLeft < 3)
	{
		RoadMiddle = BlackLineRight - 50;
	}
	// if no line on left and right side
	if ((BlackLineRight > 124) && (BlackLineLeft < 3))
	{
		RoadMiddle = 64;
	}
	
	// Store old value
	diff_old = diff;							// store old difference
	
	// Find difference from real middle
	diff = RoadMiddle - 64;						// calculate actual difference
	
	// plausibility check
	if (abs (diff - diff_old) > 50)
			{
		diff = diff_old;
			}

	// Direction Control Loop: PD Controller
	servo_position_old = servo_position;
	servo_position = KP*diff + KDP*(diff-diff_old);

	if(servo_position<-1000)
		{
			servo_position=-1000;
		}
		else if (servo_position>1000)
		{
			servo_position=1000;
		}
	
	//prevent saturation of variation of servo
		if((servo_position - servo_position_old) > 250)
		{
			servo_position = servo_position_old + 250;
		}
		else if ((servo_position - servo_position_old) < -250)
		{
			servo_position = servo_position_old - 250;
		}
		
	// Set channel 0 PWM_Servo position
	TPM1_C0V  = 8200 - servo_position ; 		// set channel 0 PWM_Servo
		
	// Set Motor Speed
	TPM0_C1V = 25;					// TPM0 channel1 left Motor 1 In 1 slow forward
	TPM0_C5V = 25;					// TPM0 channel5 right Motor 2 In 2 slow forward
	
	// red LED off
	GPIOB_PDOR |= GPIO_PDOR_PDO(1<<18);   // red LED off

}
	
// Capture LineScan Image
void ImageCapture(void)
	{
    unsigned char i;
    ADC0_CFG2 |= 0x10;							// select B side of the MUX
    TAOS_SI_HIGH;
    TAOS_DELAY;
    TAOS_CLK_HIGH;
    TAOS_DELAY;
    TAOS_SI_LOW;
    TAOS_DELAY;
    // inputs data from camera (first pixel)
	ADC0_SC1A  =  11;							// set ADC0 channel 11
	while((ADC0_SC1A & ADC_SC1_COCO_MASK) == 0);// wait until ADC is ready
	ImageData[0] = ADC0_RA;						// return value
	TAOS_CLK_LOW;

    for(i=1;i<128;i++)
    {
        TAOS_DELAY;
        TAOS_DELAY;
        TAOS_CLK_HIGH;
        TAOS_DELAY;
        TAOS_DELAY;
        // inputs data from camera (one pixel each time through loop)
    	ADC0_SC1A  =  11;							// set ADC0 channel 11
    	while((ADC0_SC1A & ADC_SC1_COCO_MASK) == 0);// wait until ADC is ready
    	ImageData[i] = ADC0_RA;						// return value
        TAOS_CLK_LOW;
    }
    
    TAOS_DELAY;
    TAOS_DELAY;
    TAOS_CLK_HIGH;
    TAOS_DELAY;
    TAOS_DELAY;
    TAOS_CLK_LOW;
}

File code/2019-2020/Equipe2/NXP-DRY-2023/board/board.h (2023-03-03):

/*
 * Copyright (c) 2015, Freescale Semiconductor, Inc.
 * Copyright 2016-2017 NXP
 *
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
 * o Neither the name of the copyright holder nor the names of its
 *   contributors may be used to endorse or promote products derived from this
 *   software without specific prior written permission.
 *
 * THIS SOFTWARE IS PROVIDED BY THE COPYRIGHT HOLDERS AND CONTRIBUTORS "AS IS" AND
 * ANY EXPRESS OR IMPLIED WARRANTIES, INCLUDING, BUT NOT LIMITED TO, THE IMPLIED
 * WARRANTIES OF MERCHANTABILITY AND FITNESS FOR A PARTICULAR PURPOSE ARE
 * DISCLAIMED. IN NO EVENT SHALL THE COPYRIGHT HOLDER OR CONTRIBUTORS BE LIABLE FOR
 * ANY DIRECT, INDIRECT, INCIDENTAL, SPECIAL, EXEMPLARY, OR CONSEQUENTIAL DAMAGES
 * (INCLUDING, BUT NOT LIMITED TO, PROCUREMENT OF SUBSTITUTE GOODS OR SERVICES;
 * LOSS OF USE, DATA, OR PROFITS; OR BUSINESS INTERRUPTION) HOWEVER CAUSED AND ON
 * ANY THEORY OF LIABILITY, WHETHER IN CONTRACT, STRICT LIABILITY, OR TORT
 * (INCLUDING NEGLIGENCE OR OTHERWISE) ARISING IN ANY WAY OUT OF THE USE OF THIS
 * SOFTWARE, EVEN IF ADVISED OF THE POSSIBILITY OF SUCH DAMAGE.
 */

#ifndef _BOARD_H_
#define _BOARD_H_

#include "clock_config.h"
#include "fsl_gpio.h"

/*******************************************************************************
 * Definitions
 ******************************************************************************/

/* The board name */
#define BOARD_NAME "FRDM-KL25Z"

/* The LPSCI to use for debug messages. */
#define BOARD_DEBUG_UART_TYPE DEBUG_CONSOLE_DEVICE_TYPE_LPSCI
#define BOARD_DEBUG_UART_BASEADDR (uint32_t) UART0
#define BOARD_DEBUG_UART_CLKSRC kCLOCK_PllFllSelClk
#define BOARD_DEBUG_UART_CLK_FREQ CLOCK_GetPllFllSelClkFreq()
#define BOARD_UART_IRQ UART0_IRQn
#define BOARD_UART_IRQ_HANDLER UART0_IRQHandler

#ifndef BOARD_DEBUG_UART_BAUDRATE
#define BOARD_DEBUG_UART_BAUDRATE 115200
#endif /* BOARD_DEBUG_UART_BAUDRATE */

/*! @brief Indexes of the TSI channels for on board electrodes */
#define BOARD_TSI_ELECTRODE_1 9U
#define BOARD_TSI_ELECTRODE_2 10U

/* Board led color mapping */
#define LOGIC_LED_ON 0U
#define LOGIC_LED_OFF 1U
#define BOARD_LED_RED_GPIO GPIOB
#define BOARD_LED_RED_GPIO_PORT PORTB
#define BOARD_LED_RED_GPIO_PIN 18U
#define BOARD_LED_GREEN_GPIO GPIOB
#define BOARD_LED_GREEN_GPIO_PORT PORTB
#define BOARD_LED_GREEN_GPIO_PIN 19U
#define BOARD_LED_BLUE_GPIO GPIOD
#define BOARD_LED_BLUE_GPIO_PORT PORTD
#define BOARD_LED_BLUE_GPIO_PIN 1U

#define LED_RED_INIT(output)                                                 \
    GPIO_WritePinOutput(BOARD_LED_RED_GPIO, BOARD_LED_RED_GPIO_PIN, output); \
    BOARD_LED_RED_GPIO->PDDR |= (1U << BOARD_LED_RED_GPIO_PIN) /*!< Enable target LED_RED */
#define LED_RED_ON() \
    GPIO_ClearPinsOutput(BOARD_LED_RED_GPIO, 1U << BOARD_LED_RED_GPIO_PIN) /*!< Turn on target LED_RED */
#define LED_RED_OFF() \
    GPIO_SetPinsOutput(BOARD_LED_RED_GPIO, 1U << BOARD_LED_RED_GPIO_PIN) /*!< Turn off target LED_RED */
#define LED_RED_TOGGLE() \
    GPIO_TogglePinsOutput(BOARD_LED_RED_GPIO, 1U << BOARD_LED_RED_GPIO_PIN) /*!< Toggle on target LED_RED */

#define LED_GREEN_INIT(output)                                                   \
    GPIO_WritePinOutput(BOARD_LED_GREEN_GPIO, BOARD_LED_GREEN_GPIO_PIN, output); \
    BOARD_LED_GREEN_GPIO->PDDR |= (1U << BOARD_LED_GREEN_GPIO_PIN) /*!< Enable target LED_GREEN */
#define LED_GREEN_ON() \
    GPIO_ClearPinsOutput(BOARD_LED_GREEN_GPIO, 1U << BOARD_LED_GREEN_GPIO_PIN) /*!< Turn on target LED_GREEN */
#define LED_GREEN_OFF() \
    GPIO_SetPinsOutput(BOARD_LED_GREEN_GPIO, 1U << BOARD_LED_GREEN_GPIO_PIN) /*!< Turn off target LED_GREEN */
#define LED_GREEN_TOGGLE() \
    GPIO_TogglePinsOutput(BOARD_LED_GREEN_GPIO, 1U << BOARD_LED_GREEN_GPIO_PIN) /*!< Toggle on target LED_GREEN */

#define LED_BLUE_INIT(output)                                                  \
    GPIO_WritePinOutput(BOARD_LED_BLUE_GPIO, BOARD_LED_BLUE_GPIO_PIN, output); \
    BOARD_LED_BLUE_GPIO->PDDR |= (1U << BOARD_LED_BLUE_GPIO_PIN) /*!< Enable target LED_BLUE */
#define LED_BLUE_ON() \
    GPIO_ClearPinsOutput(BOARD_LED_BLUE_GPIO, 1U << BOARD_LED_BLUE_GPIO_PIN) /*!< Turn on target LED_BLUE */
#define LED_BLUE_OFF() \
    GPIO_SetPinsOutput(BOARD_LED_BLUE_GPIO, 1U << BOARD_LED_BLUE_GPIO_PIN) /*!< Turn off target LED_BLUE */
#define LED_BLUE_TOGGLE() \
    GPIO_TogglePinsOutput(BOARD_LED_BLUE_GPIO, 1U << BOARD_LED_BLUE_GPIO_PIN) /*!< Toggle on target LED_BLUE */

#define BOARD_ACCEL_I2C_BASEADDR I2C0

/* ERPC SPI configuration */
#define ERPC_BOARD_SPI_BASEADDR SPI0
#define ERPC_BOARD_SPI_BAUDRATE 500000U
#define ERPC_BOARD_SPI_CLKSRC SPI0_CLK_SRC
#define ERPC_BOARD_SPI_CLK_FREQ CLOCK_GetFreq(SPI0_CLK_SRC)
#define ERPC_BOARD_SPI_INT_GPIO GPIOD
#define ERPC_BOARD_SPI_INT_PORT PORTD
#define ERPC_BOARD_SPI_INT_PIN 0U
#define ERPC_BOARD_SPI_INT_PIN_IRQ PORTD_IRQn
#define ERPC_BOARD_SPI_INT_PIN_IRQ_HANDLER PORTD_IRQHandler

/* DAC base address */
#define BOARD_DAC_BASEADDR DAC0

/* Board accelerometer driver */
#define BOARD_ACCEL_MMA
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

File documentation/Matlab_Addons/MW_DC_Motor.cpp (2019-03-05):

#include "MW_DC_Motor.h"
#include "mbed.h"
#include "MW_target_hardware_resources.h"

DigitalOut MW_DC_Motor::hBridgeEN(PTE21);

MW_DC_Motor::~MW_DC_Motor() {
    disableHbridge();
    delete this->motorIn1;
    delete this->motorIn2;
}

MW_DC_Motor::MW_DC_Motor(char motorLetter) {
    disableHbridge();

    switch( motorLetter ) {
        default:
            break;

        case 'A':
            this->motorIn1 = new PwmOut(PTA4);
            this->motorIn2 = new PwmOut(PTA5);

            break;

        case 'B':
            this->motorIn1 = new PwmOut(PTC8);
            this->motorIn2 = new PwmOut(PTC9);

            break;
    }
    
    initMotorInput(this->motorIn1);
    initMotorInput(this->motorIn2);
    enableHbridge();
}

void MW_DC_Motor::initMotorInput(PwmOut* motorIn) {
    motorIn->period(1.0/MW_TPM0_FREQUENCY);
    motorIn->write(0.0);
}

void MW_DC_Motor::setSpeed(float speed) {
    if(speed > 1.0)
        speed = 1.0;
    else if(speed < -1.0)
        speed = -1.0;

    if(speed >= 0) {
        *(this->motorIn1) = speed;
        *(this->motorIn2) = 0.0;
    } else if(speed < 0) {
        *(this->motorIn1) = 0.0;
        *(this->motorIn2) = -speed;
    }
}

void MW_DC_Motor::disableHbridge() {
    this->hBridgeEN = false;
}

void MW_DC_Motor::enableHbridge() {
    this->hBridgeEN = true;
}

float MW_DC_Motor::getSpeed() {

    return this->motorIn1->read() - this->motorIn2->read();
}
    
MW_DC_Motor& MW_DC_Motor::operator= (float speed) { 
    setSpeed(speed);
    return *this;
}

MW_DC_Motor& MW_DC_Motor::operator= (MW_DC_Motor& rhs) {
    setSpeed(rhs.getSpeed());
    return *this;
}

MW_DC_Motor::operator float() {
    return getSpeed();
}

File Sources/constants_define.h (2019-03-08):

#ifndef CONSTANTS_DEFINE_H
#define CONSTANTS_DEFINE_H

#include "derivative.h" /* include peripheral declarations */
#include "math.h"	/* used for different calculations, including the difference of Gaussian with roots, exponential and PI */



/*	MAIN DEFINITIONS */

/* Initialisations (beginning of the code) */
#define PRESCALER_TPM0			3						// prescaler for TPM0 (Motor)
#define PRESCALER_TPM1			3						// prescaler for TPM1 (Servo)

#define MODULO_TPM0				600						// modulo TPM0 (Motor)
#define MODULO_TPM1				6000					// modulo TPM1 (Servo)

#define TPM0_SPEED_INIT			150						//	TPM0 channel1 left Motor 1 In 1 slow forward
#define TPM1_SPEED_INIT			150						//	TPM0 channel5 right Motor 2 In 2 slow forward


// Defines for Direction PD Servo Control Loop
#define KP						50			// Proportional coefficient
#define KDP						25			// Differential coefficient

#define SERVO_BASE 				7800		// initial position for the servo (center)


/* 
*
*	CAMERA DEFINITIONS
*
*/

// Defines for LineScan Camera
#define TAOS_DELAY				asm ("nop")				// minimal delay time
#define	TAOS_SI_HIGH			GPIOB_PDOR |= (1<<8)	// SI on PTB8
#define	TAOS_SI_LOW				GPIOB_PDOR &= ~(1<<8)	// SI on PTB8
#define	TAOS_CLK_HIGH			GPIOB_PDOR |= (1<<9)	// CLK on PTB9
#define	TAOS_CLK_LOW			GPIOB_PDOR &= ~(1<<9)	// CLK on PTB9


// Define thresholds for Camera Black Line recognition
#define THRESHOLD_HIGH				140			// Higher threshold : does not capture noise but may not capture all maximums.
#define THRESHOLD_LOW				50			// Lower threshold : May capture more maximums than High threshold but can capture noise too.

#define THRESHOLD_CLASSIC			120			// standard threshold : used in the basic image processing function

#define FUNCTIONNING_MODE			2			// operating mode: from 1 to 3: algorithm more and more precise but heavy

#define SIGMA_1	 					2			// square root of the variance for the first gaussian filter
#define SIGMA_2 					2.5			// square root of the variance for the second gaussian filter. 

#define PI							3.14159265358979323846		// value of PI









// Defines for speed coefficients (differential)
#define L_TURN_R_LANE_THRESHOLD		70
#define L_TURN_L_LANE_THRESHOLD		10
#define R_TURN_R_LANE_THRESHOLD		120
#define R_TURN_L_LANE_THRESHOLD		35
#define END_L_LANE_THRESHOLD		30
#define END_R_LANE_THRESHOLD		100

#define L_TURN_L_MOTOR_SPEED		80
#define L_TURN_R_MOTOR_SPEED		80
#define R_TURN_L_MOTOR_SPEED		80
#define R_TURN_R_MOTOR_SPEED		80

#define FORWARD_MOTOR_SPEED			150


#endif /* CONSTANTS_DEFINE_H */

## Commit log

2019-01-30 actually blink the led this time
2019-02-16 Implement code for the encoders
2019-02-16 implement servoMotor .c and .h
2019-02-21 Adaptateur camera fini
    [Adaptateur_Camera.kicad_pcb, Adaptateur_Camera.sch, Carte_Puissance.dxf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]
2019-02-21 Correction sur l'adaptateur Camera / Ajout du pcb de l'encodeur optique
    [Adaptateur_Camera.kicad_pcb, Adaptateur_Camera.sch]
2019-02-25 added camera tests algorithms
2019-02-26 Updated camera test algorithm
2019-02-27 Encoder OK, Camera OK
    [Adaptateur_Camera.kicad_pcb, Encodeur_Optique.kicad_pcb, Encodeur_Optique.sch]
2019-03-09 fix minor mistakes from the precedent commit
    [camera.c, camera.h, constants_define.h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]
2019-07-23 reorganisation des repertoires + mise a jour du fichier .gitignore
    [Adaptateur_Camera2.kicad_pcb, Adaptateur_Camera2.sch]
2019-07-29 Essai de Freecad, pas concluant
    [Alamak.FCStd, Carte_puissance.kicad_pcb, Carte_puissance.sch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]
2019-07-30 Modele créé sous Inventor
    [ANSI B 18.2.4.1 M - M2,5 x 0,45Style 1.ipt, ANSI B 18.2.4.1 M - M3 x 0,5Style 1.ipt, ANSI B 18.2.4.1 M - M3 x 0,5Style 2.ipt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]
2019-07-30 Ajout de fichiers DXF et DWG
    [PCBCapteurs.dwg, PCBCapteurs.dxf, PCBPuissance.dwg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]
2019-07-31 Modelisation sous Inventor bien avancée: manque la camera
    [Alamak.iam, Base.ipt, Fusée.ipt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]
2019-07-31 Corrections mineures
    [Alamak.iam, PareChoc.ipt]
2019-07-31 Cartes En cours de conception
    [Carte_Capteurs.kicad_pcb, Carte_Capteurs.sch, Carte_puissance.kicad_pcb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]
2019-08-29 demarrage carte capteurs
    [Carte_Capteurs.kicad_pcb, Carte_Capteurs.sch, Carte_Capteurs.step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]
2019-08-29 Mise a jour FRDM-KL25Z step
    [Carte Capteurs.iam, FRDM-KL25Z.ipt, FRDM-KL25Z.stp]
2019-08-29 Petites corrections
    [Alamak.iam, Carte_Capteurs.ipt, Carte_Puissance.iam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]
2019-08-29 version d'echange
    [Carte_Capteurs.kicad_pcb, Carte_Capteurs.sch]
2019-08-29 Ajout du XBEE
    [Alamak.iam, Xbee.ipt, Xbee.stp]
2019-09-04 sauvegarde intermediaire
    [3386P001XXX-EY5.stp, 3386p001xxx-ey5.igs, Carte_Capteurs.kicad_pcb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]
2019-09-05 Cartes terminées
    [Carte_Capteurs.kicad_pcb, Carte_Capteurs.sch, Carte_puissance.kicad_pcb]
2019-09-05 ajout des versions sur les cartes
    [Carte_Capteurs.kicad_pcb, Carte_puissance.kicad_pcb, Carte_puissance.sch]
2019-09-06 Ajout des bon rendu des cartes puissance et capteurs, mais crash d'inventor
    [Alamak.iam]
2019-09-18 leger evolution sur PCB de la carte de puissance
    [Carte_puissance.kicad_pcb]
2019-10-03 mise a jour des projets Kicad
2019-10-11 Correction sur carte capteur + realisation des pieces du circuit sous LibreCad/InkScape
    [Carte_Capteurs.kicad_pcb, Carte_Capteurs.sch, Carte_puissance.sch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]
2019-10-18 correction sur carte capteur
    [Carte_Capteurs.kicad_pcb, Carte_Capteurs.sch]
2019-11-28 Added schematic in pdf format
2019-11-28 Added schematic
2019-12-03 debut : led rgb et afficheur 7 segments
2019-12-03 updated .gitignore for CodeWarrior files & fixes 7segment driver issues
    [main.c]
2019-12-03 7segment driver simulated correct -> to test on the car
    [kinetis_sysinit.c]
2019-12-04 ring buffer and debug uart transmit working ! Also PLL is fixed at 48MHz
    [main.c]
2019-12-05 uart and 7segment display complete
2019-12-07 defines for uart type
2019-12-07 created motor test project
2019-12-07 moved motor
2019-12-07 only one pwm channel working
2019-12-08 Motor still not working update
    [Motor.c, Motor.h, camera.c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]
2019-12-08 servo rework
2019-12-10 motor enable and direction fixed, right motor still not moving
    [Motor.c, Motor.h, main.c]
2019-12-10 removed debug class from servo project
2019-12-10 added encoder project
2019-12-27 motor working !
2019-12-27 servo funcs
2019-12-28 modified readme and servo wrapup
2020-01-17 creation d'une carte camera et d'une carte pour els led
    [Carte_Camera.kicad_pcb, Carte_Camera.sch, Carte_Capteurs.kicad_pcb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]
2020-01-22 -mcreated image processing folder
    [sample_data.xlsx]
2020-01-23 Config encoders
2020-01-28 -mupdates encoder calculations and arr values
2020-01-29 removed extra encoder project
2020-01-29 updated Encoder to use class and return acutal speed
2020-01-30 ajout de la carte chassi DFRobotics + creation d'une nouvelle carte led + creation d'une carte capteur pour DFRobotic + correction de l'alimentation en 5V des encodeurs sur DFRobotic (carte Landzo a 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
    [Carte_Camera.kicad_pcb, Carte_Camera.sch, Carte_Capteurs-extensions.sch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]
2020-01-30 Branche evolution-HW a merger sur evo60
    [Alamak.iam, EquerrePCBDroite.stp, EquerrePCBGauche.stp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]
2020-01-30 Reorganisation du repertoire PCB + generation des pdf des schemas
    [Adaptateur_Camera.kicad_pcb, Adaptateur_Camera.sch, Carte_Camera.kicad_pcb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]
2020-01-30 Suppression de fichiers backup et doublons
    [Adaptateur_Camera2.kicad_pcb, Adaptateur_Camera2.sch]
2020-02-01 movement intergrating encoder
2020-02-03 graph vitesse/PWM
    [Gain_moteur_encodeur.ods]
2020-02-04 recharge battery
    [differential.ods]
2020-02-05 low power timer config
2020-02-06 Ajout des regles NXP Cup pour 2020 (V1) + modifs mineures sur pcbs
    [Carte_Capteurs.kicad_pcb, Carte_Capteurs.sch, Carte_Chassis_DFRobotic.kicad_pcb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]
2020-02-06 Ajout des regles NXPCup 2020 (V1)
2020-02-06 shared drivers folder
2020-02-06 lptmr + battery
2020-02-07 macro LED camera
2020-02-07 Changement de capteur pour les encodeurs DFRobot
    [Encodeurs-DFRobotics.kicad_pcb, Encodeurs-DFRobotics.sch]
2020-02-13 servo calibration
2020-02-13 servo excel
    [servo_tests.xlsx]
2020-03-01 push NXP_Dry Equipe 2
    [Adaptateur_Camera.kicad_pcb, Adaptateur_Camera.sch, Carte_Camera.kicad_pcb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]
2024-01-27 ADDED LiDAR
2024-01-31 STABLE : LiDAR
